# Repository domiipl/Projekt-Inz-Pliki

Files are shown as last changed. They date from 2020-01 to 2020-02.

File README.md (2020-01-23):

# Wstęp i informacje o projekcie
Cześć, jesteśmy grupą studentów, którzy na swój projekt inżynierski postanowili stworzyć niedużego robota sterowanego za pomocą interaktywnej maty.

Robot sterowany jest za pomocą sekwencji, które wprowadzamy na wyżej wymienionej macie. Możemy dawać mu proste komendy pozwalające na poruszanie się. Alternatywnym trybem jest jazda swobodna pozwalająca na sterowanie robotem w czasie rzeczywistym. Mata jest urządzeniem posiadającym układ przycisków 4x4 i ekran pokazujący aktualnie wpisywaną sekwencję. Posiadając podstawową wiedzę na temat programowania i elektroniki, będziesz mógł skonstruować taki zestaw sam, w zaciszu swojego domu. 

Bardziej szczegółowe informacje na temat samego projektu znajdziesz w samym poradniku.

Repozytorium jest podzielone na pięć folderów.
Dzielą się one na:
* **Kod robota** - znajduje się tu gotowy kod, dzięki któremu robot będzie w stanie się poruszać.
* **Kod maty** - znajduje się tu gotowy kod, dzięki któremu będziemy w stanie wysyłać komendy z maty do robota.
* **Schemat robota** - wymagane pliki do zamówienia płytki pcb do robota.
* **Schemat maty** - wymagane pliki do zamówienia płytki pcb do robota.
* **Instruktaż** - szczegółowy poradnik zawierający wymagane materiały oraz opis budowy robota i maty.

Zalecamy z zapoznaniem się dokładnie z poradnikiem przed próbą konstrukcji. Spis treści znajdziesz w pliku README w folderze "Instruktaż".

Powodzenia!

Chcielibyśmy tutaj jeszcze dodać, że wykonując projekt trzeba liczyć się z pewnymi wydatkami.
Orientacyjne koszty na dzień 16 stycznia 2020:
* **Robot** - Koszt wszystkich części robota to około 130zł, jeśli kupujemy na botlandzie. Można zmniejszyć koszta kupując części na przykład na aliexpress, jednak wydłuży to czas w jakim części do nas przyjdą.
* **Mata** - Koszt wszystkich części maty wynosi około 205zł, podobna sytuacja jak z częściami u robota, koszty można zmniejszyć kupując na przykład z allegro lub aliexpress.

Zdjęcia końcowe produktów:

**Robot**

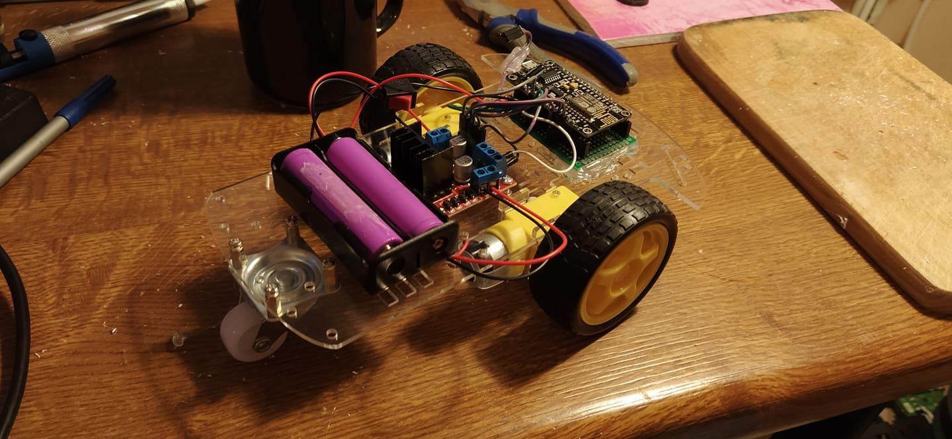
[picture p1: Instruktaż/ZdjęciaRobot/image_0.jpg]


**Mata**

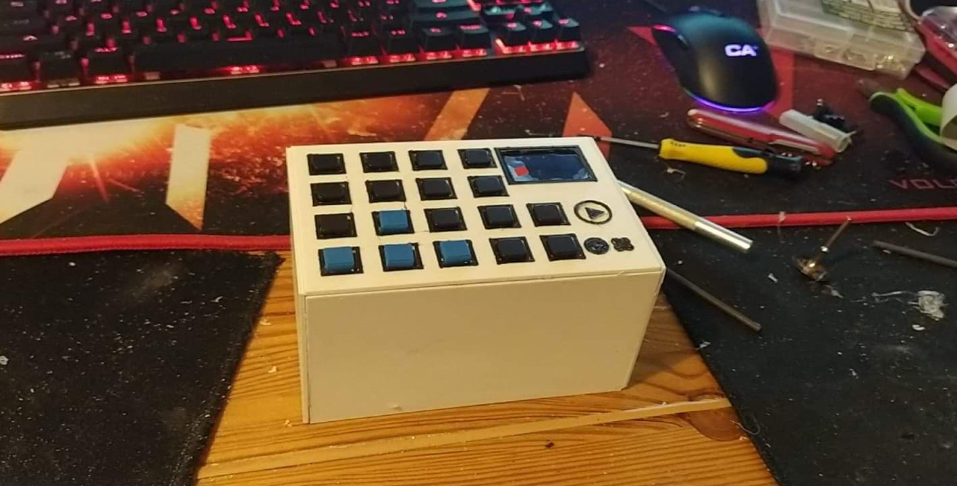
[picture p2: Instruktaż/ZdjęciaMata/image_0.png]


Filmy przedstawiające działanie projektu:

[Tryb komend](https://www.youtube.com/watch?v=S5_3_hodGV8)

[Tryb swobodny](https://www.youtube.com/watch?v=uaEHo7fgwFo)

W razie problemów, możesz kontaktować się z nami pod tym adresem e-mail:
## **projektinzrobot@gmail.com**

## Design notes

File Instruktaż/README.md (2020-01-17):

### Zalecamy czytanie poradnika zgodnie z kolejnością spisu treści

# Spis treści
1. [Informacje o projekcie](https://github.com/domiipl/Projekt-Inz-Pliki/blob/master/Instrukta%C5%BC/Informacje.md)
2. [Przygotowanie](https://github.com/domiipl/Projekt-Inz-Pliki/blob/master/Instrukta%C5%BC/Przygotowanie.md)
    - NodeMCU(Arduino)
      - Arduino IDE
      - Konfiguracja IDE
    - Raspberry Pi Zero
      - Instalacja Node.js
    - Części do budowy robota oraz maty
    - Płytki PCB
      - Schematy
      - Wymagane materiały
      - Tworzenie płytki
    - Pistolet do kleju
    - Lutownica kolbowa
    - Śrubokręt i śrubki
3. [Robot](https://github.com/domiipl/Projekt-Inz-Pliki/blob/master/Instrukta%C5%BC/Robot.md)
    - Lista wymaganych materiałów
    - Budowa Robota
    - Kod do robota
        - Instalacja kodu
        - Opis kodu
4. [Mata](https://github.com/domiipl/Projekt-Inz-Pliki/blob/master/Instrukta%C5%BC/Mata.md)
    - Lista wymaganych materiałów
    - Budowa maty
      - Obudowa maty
    - Kod do maty
      - Instalacja kodu
      - Opis kodu
5. [Połączenie](https://github.com/domiipl/Projekt-Inz-Pliki/blob/master/Instrukta%C5%BC/Po%C5%82%C4%85czenie.md)
    - Opis działania
6. [Podsumowanie](https://github.com/domiipl/Projekt-Inz-Pliki/blob/master/Instrukta%C5%BC/Podsumowanie.md)
    - Dodatkowe pomysły

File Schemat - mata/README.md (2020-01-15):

# Pliki potrzebne podczas zamawiania płytek PCB przez internet.
**Najważniejszym jest plik spakowany, ponieważ zawiera kilka istotnych plików do zamówienia internetowego.**

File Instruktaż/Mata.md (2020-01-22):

# 4. **Mata sterująca**



## **Lista wymaganych materiałów:**

1. **Raspberry Pi Zero W 512MB RAM - WiFi + BT 4.1** - 1 sztuka
<p align="center">
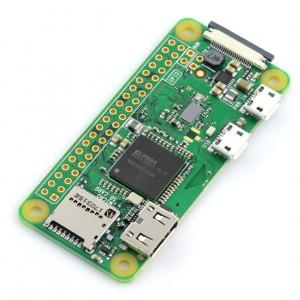
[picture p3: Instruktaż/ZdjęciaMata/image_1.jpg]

</p>

**Przykładowy link do sklepu:**

[https://botland.com.pl/pl/moduly-i-zestawy-raspberry-pi-zero/8330-raspberry-pi-zero-w-512mb-ram-wifi-bt-41.html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](https://botland.com.pl/pl/moduly-i-zestawy-raspberry-pi-zero/8330-raspberry-pi-zero-w-512mb-ram-wifi-bt-41.html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) 

[https://botland.com.pl/pl/gniazda-szpilkowe-goldpin/12659-wtyk-goldpin-2x20-prosty-raster-254mm.html](https://botland.com.pl/pl/gniazda-szpilkowe-goldpin/12659-wtyk-goldpin-2x20-prosty-raster-254mm.html) 

2. **Płytka uniwersalna:**
<p align="center">
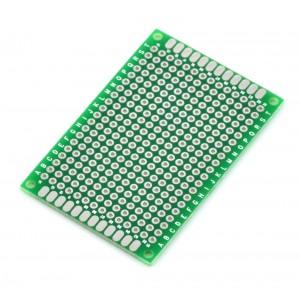
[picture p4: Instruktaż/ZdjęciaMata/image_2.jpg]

</p>

**Przykładowy link do sklepu:** 

[9cm x 15cm](https://www.gotronik.pl/uniwersalna-plytka-drukowana-pcb-9x15cm-1836-otworow-pol-kontaktowych-p-1273.html)
[2cm x 8cm](https://www.gotronik.pl/uniwersalna-plytka-drukowana-pcb-2x8cm-168-otworow-pol-kontaktowych-p-1268.html)

Wymiary minimalne:  9cm x 15cm

Komentarz: + dodatkowa 2cm x 8cm do budowy płytki zasilającej

3. **Części do płytki drukowanej:**

**Przykładowy link do sklepu:** 

[https://botland.com.pl/pl/laminaty/1054-laminat-fr4-dwustronny-rozmiar-l.html](https://botland.com.pl/pl/laminaty/1054-laminat-fr4-dwustronny-rozmiar-l.html) 

[https://botland.com.pl/pl/laminaty/1943-laminat-dwustronny-150x210mm.html](https://botland.com.pl/pl/laminaty/1943-laminat-dwustronny-150x210mm.html)[ ](https://botland.com.pl/pl/laminaty/1943-laminat-dwustronny-150x210mm.html)

[https://botland.com.pl/pl/wytrawiacze/1057-wytrawiacz-b327-100g-5901764329183.html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](https://botland.com.pl/pl/wytrawiacze/1057-wytrawiacz-b327-100g-5901764329183.html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) 

4. **Zasilanie do RPi - L7805CV** - 1 sztuka.
<p align="center">
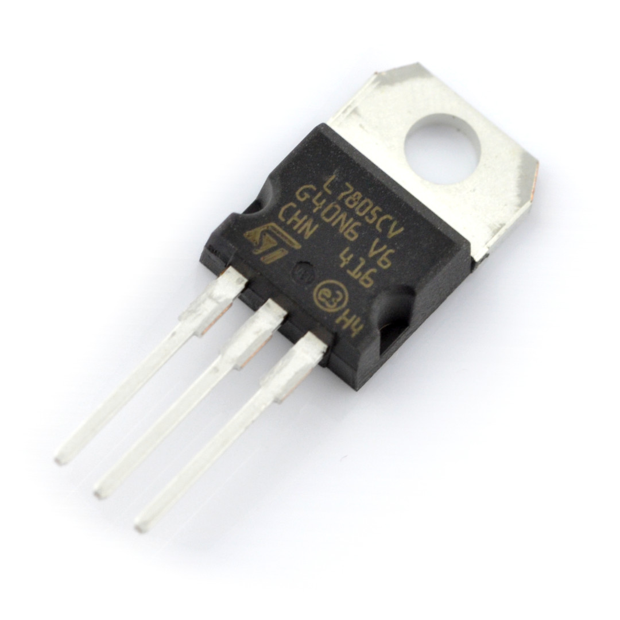
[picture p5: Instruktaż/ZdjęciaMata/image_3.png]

</p>

**Przykładowy link do sklepu:**

[https://abc-rc.pl/product-pol-6839-Elektronika-Stabilizator-L7805CV-5V-1-5A-obudowa-TO-220.html](https://abc-rc.pl/product-pol-6839-Elektronika-Stabilizator-L7805CV-5V-1-5A-obudowa-TO-220.html)

* Napięcie wyjściowe: 5V
* Maksymalne napięcie wejściowe: 35V
* Prąd wyjściowy: 1,5A
* Liczba pinów: 3
* Obudowa: TO-220
* Nr katalogowy: SNL7805CV

5. **Baterie - Model: "18650"** - 1 sztuka.
<p align="center">
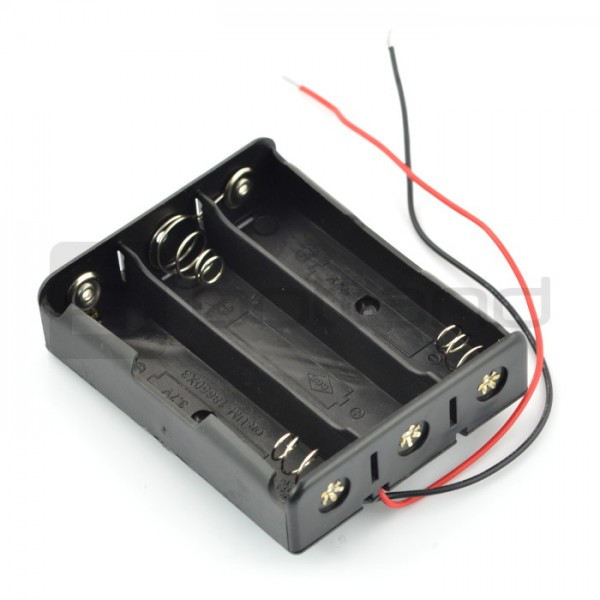
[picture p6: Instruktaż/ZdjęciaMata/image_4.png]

</p>
[https://botland.com.pl/pl/koszyki-na-baterie/5241-koszyk-na-3-baterie-typu-18650.html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](https://botland.com.pl/pl/koszyki-na-baterie/5241-koszyk-na-3-baterie-typu-18650.html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)  

[https://www.gotronik.pl/akumulator-li-ion-18650-ogniwo-litowo-jonowe-3400-mah-panasonic-ncr-18650b-p-6931.html](https://www.gotronik.pl/akumulator-li-ion-18650-ogniwo-litowo-jonowe-3400-mah-panasonic-ncr-18650b-p-6931.html)

(same baterie można dużo taniej znaleźć na Allegro lub OLX)

6. **Wtyk goldpin 2x40 prosty raster 2,54mm** - 1 raster powinien wystarczyć. 
<p align="center">
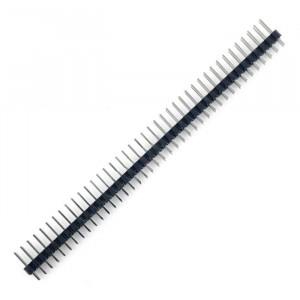
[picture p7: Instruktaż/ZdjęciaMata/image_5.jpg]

</p>

**Przykładowy link do sklepu:** 

[https://botland.com.pl/pl/gniazda-szpilkowe-goldpin/204-wtyk-goldpin-2x40-prosty-raster-254mm.html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](https://botland.com.pl/pl/gniazda-szpilkowe-goldpin/204-wtyk-goldpin-2x40-prosty-raster-254mm.html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)

7. **Tact Switch 12x12mm z nasadką**- 18 sztuk
<p align="center">
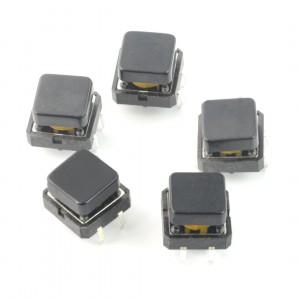
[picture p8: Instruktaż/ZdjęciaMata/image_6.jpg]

</p>

**Przykładowy link do sklepu:**

[https://botland.com.pl/pl/tact-switch/11138-tact-switch-12x12mm-z-nasadka-kwadrat-czarny-5szt.html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](https://botland.com.pl/pl/tact-switch/11138-tact-switch-12x12mm-z-nasadka-kwadrat-czarny-5szt.html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) 

8. **Wyświetlacz OLED niebieski graficzny 1,3'' 128x64px I2C v2** - 1 sztuka.
<p align="center">
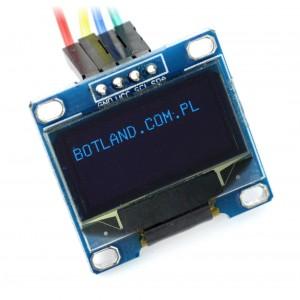
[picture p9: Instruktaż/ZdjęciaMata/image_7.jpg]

</p>

* Napięcie pracy: od 3,3 V do 5,0 V
* Sterownik: SH1106 (dokumentacja)
* Komunikacja: I2C
* Typ wyświetlacza: OLED
* Przekątna: 1,3"
* Rozdzielczość: 128 x 64 px
* Kolor znaków: biały
* Kąt widzenia: powyżej 160 °
* Temperatura pracy: od -20 °C do 70 °C
* Wymiary: 35 x 33 mm

**Przykładowy link do sklepu:**

[https://botland.com.pl/pl/wyswietlacze-oled/8246-wyswietlacz-oled-niebieski-graficzny-13-128x64px-i2c-v2-niebieskie-znaki.html](https://botland.com.pl/pl/wyswietlacze-oled/8246-wyswietlacz-oled-niebieski-graficzny-13-128x64px-i2c-v2-niebieskie-znaki.html)

## **Budowa maty**

Na wstępie chciałbym zaznaczyć, że uniwersalne płytki PCB dają nam ogromną swobodę w tym jak nasz efekt końcowy będzie się prezentować. 

Przed rozpoczęciem budowy "maty" najlepiej zapoznać się z schematem i wstępnie zaplanować sobie rozkład połączeń na uniwersalnej płytce. Porządek to podstawa, ponieważ później pozwoli nam to na łatwe modyfikacje i naprawy ewentualnych błędów.

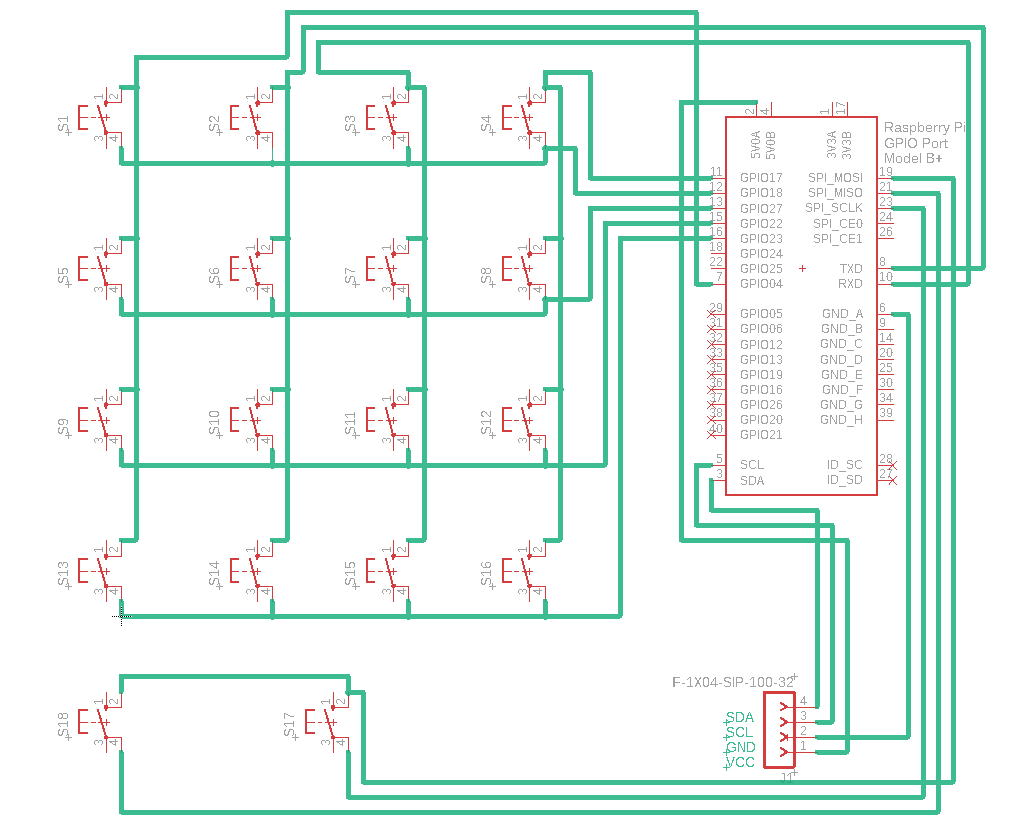
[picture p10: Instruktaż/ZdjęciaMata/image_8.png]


Pierwszym krokiem będzie rozkład przycisków S1 - S16. 

Z racji tego, że wybrana płytka jest dosyć dużych rozmiarów, bo ma aż 9cm na 15cm, to możemy pozwolić sobie na spore odstępy między przyciskami tak jak na poniższym zdjęciu (oczywiście każdy może mieć większe bądź mniejsze odstępy, to już według osobistych preferencji):

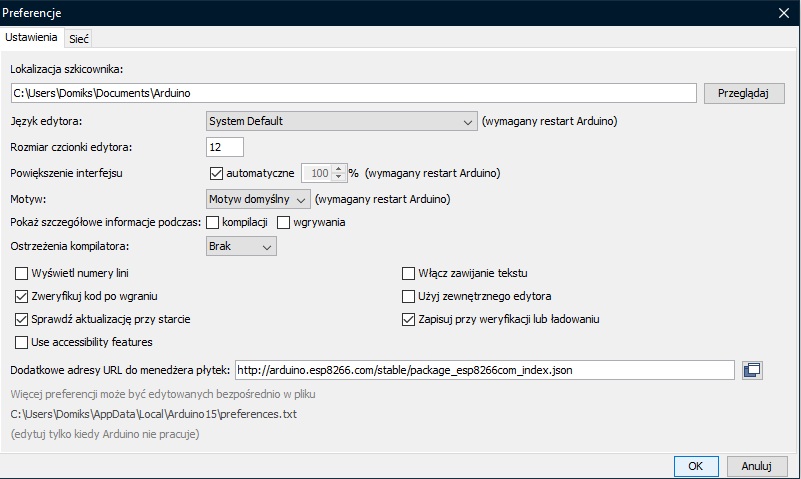
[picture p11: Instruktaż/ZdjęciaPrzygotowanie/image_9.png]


Następnie możemy dodać kolejne dwa przyciski (S17 i S18), które będą przyciskami funkcyjnymi: 



Teraz gdy już mamy zaplanowane rozłożenie przycisków możemy przejść do przypomnienia sobie schematu samej klawiatury jak i samego przycisku co ułatwi nam lutowanie. 

- Klawiatura:

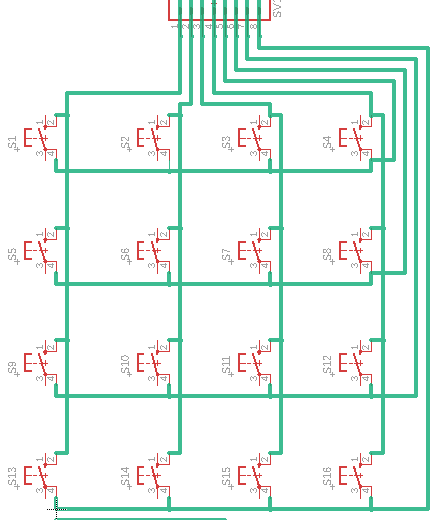
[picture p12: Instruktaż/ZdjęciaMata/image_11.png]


- Przycisk: 

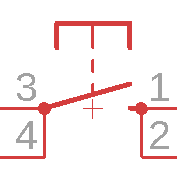
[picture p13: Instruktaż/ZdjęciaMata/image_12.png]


Podstawową rzeczą jaką powinniśmy zauważyć patrząc na schemat przycisku jest fakt, że nóżki 3 i 4 oraz 1 i 2 są ze sobą połączone, więc wciśnięcie przycisku powoduje zamknięcie obwodu między parami nóżek 1,2 i 3,4. Jest to o tyle istotny fakt, że podczas lutowania możemy zaoszczędzić bardzo dużo miejsca jak i czasu poświęconego na pracę. Przejdźmy zatem do lutowania: 

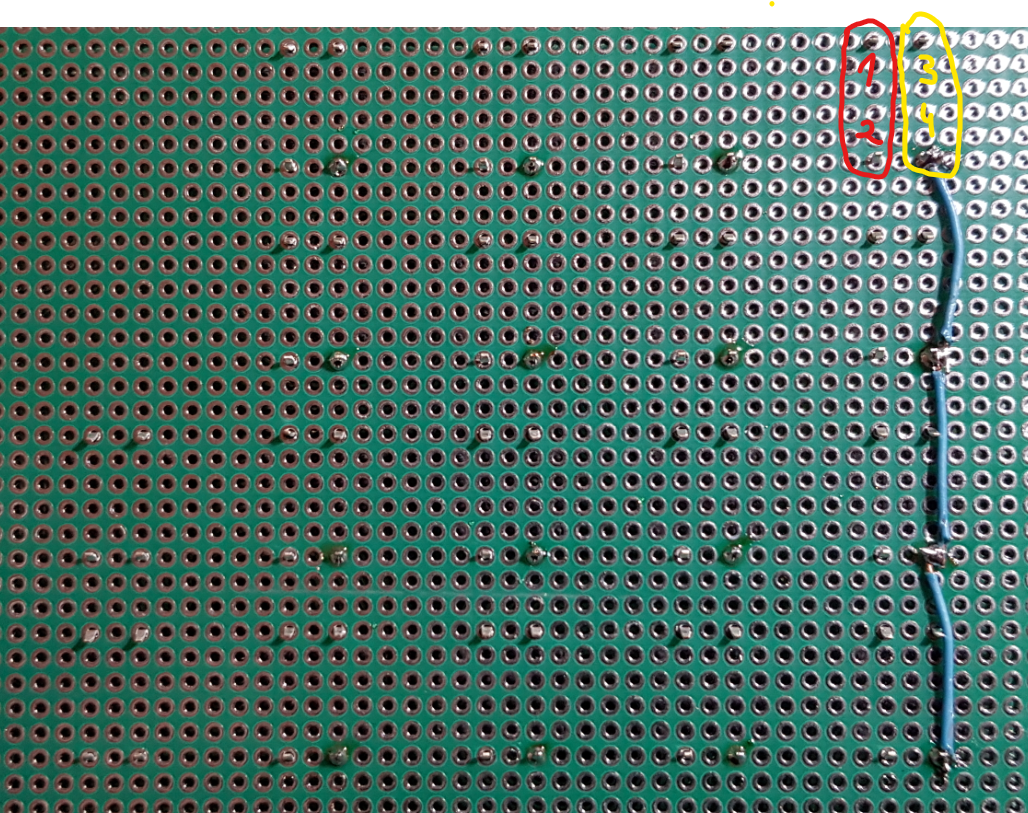
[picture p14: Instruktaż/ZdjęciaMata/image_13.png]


Na zdjęciu powyżej widzimy pierwszą zlutowaną kolumnę. Oczywiście można było zrobić to inaczej, ale tak jak wspominałem, na płytkach uniwersalnych mamy pełną dowolność.

Poniżej zdjęcia będą przedstawiać postęp w lutowaniu kolumn i wierszy między przyciskami. 







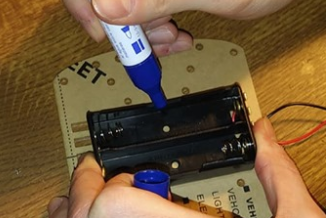
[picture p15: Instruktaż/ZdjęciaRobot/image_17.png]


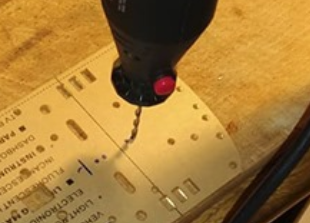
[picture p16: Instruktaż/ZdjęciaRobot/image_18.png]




Następnie aby sprawdzić czy wszystko zostało podłączone tak jak należy oraz udało nam się uniknąć "zimnych lutów" możemy na szybko podłączyć klawiaturę do np. Arduino i sprawdzić czy działa poprawnie: 

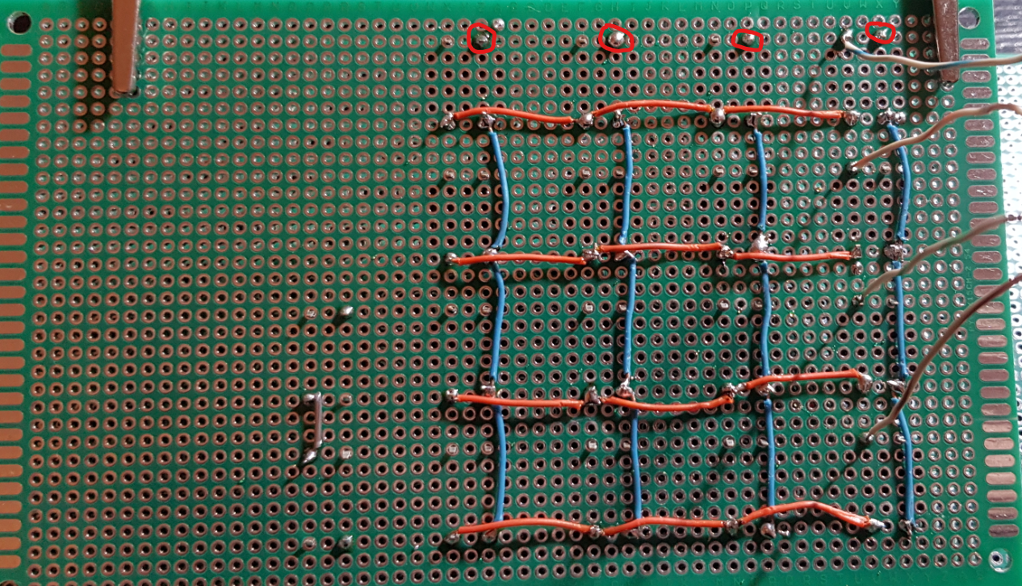
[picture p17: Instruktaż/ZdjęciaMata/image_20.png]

(Na czerwono są zaznaczone miejsca w których zostały przylutowane kable od kolumn, a nie ma ich na zdjęciu)


Powyżej widać klawiaturę podpiętą do Arduino, 

a poniżej widać program oraz wynik na konsoli po naciśnięciu klawiszy. 

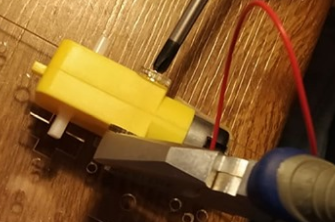
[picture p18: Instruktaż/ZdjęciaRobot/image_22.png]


(Kod do Arduino zostanie udostępniony na GitHubie jako plik [test_klawiatury_4x4](https://github.com/domiipl/Projekt-Inz-Pliki/blob/master/Kod%20-%20mata/test_klawiatury_4x4.ino))

Po poprawnych wynikach otrzymanych w teście możemy przejść do dodania pinów do klawiatury aby później można było ją podłączyć do RPi Zero. 
(Nie zastosowałem tutaj kabli przylutowanych na stałe, ponieważ nie miałem odpowiednich pod ręką, a kabelki ze skrętki nie były odpowiednie, ponieważ szybko się łamały i były zbyt sztywne)

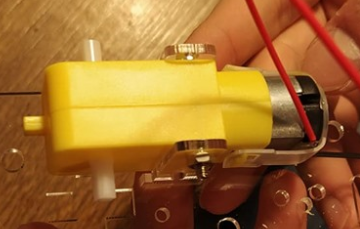
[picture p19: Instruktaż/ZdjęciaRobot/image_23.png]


Powyżej można zauważyć 4 dodatkowe piny obok przycisków funkcyjnych, ponieważ w międzyczasie został przylutowany ekran OLED co będzie widoczne na następnym zdjęciu: 


Po skończonej klawiaturze możemy przejść do zasilania jakiego użyjemy dla naszego Raspberry Pi Zero. 

Ważne jest to aby pamiętać o podstawowych parametrach jakie trzeba zapewnić RPi aby działało stabilnie. Po pierwsze najważniejsze jest napięcie, jeśli chcemy zasilić RPi poprzez złącze microUSB to musimy zapewnić następujące wartości: 

* Napięcie [V]:  4.75 - 5.25
* Natężenie [mA]: min. 500

Jest również możliwość zasilania RPi poprzez GPIO, ale jest to dosyć ryzykowny zabieg. 

Do wykonania prostego zasilacza będziemy potrzebowali: 

* L7805CV
* Koszyk na baterie 3x 18650
* kawałek płytki uniwersalnej
* trochę kabla 
* przełącznik 
* kondensator (ja wybrałem 10v 470uF)
* oraz opcjonalnie można użyć złącz ARK

Na wstępie mały obrazek z wyjściami dla L7805CV aby wszystko poprawnie podłączyć: 



Następnie schemat całego zasilacza:

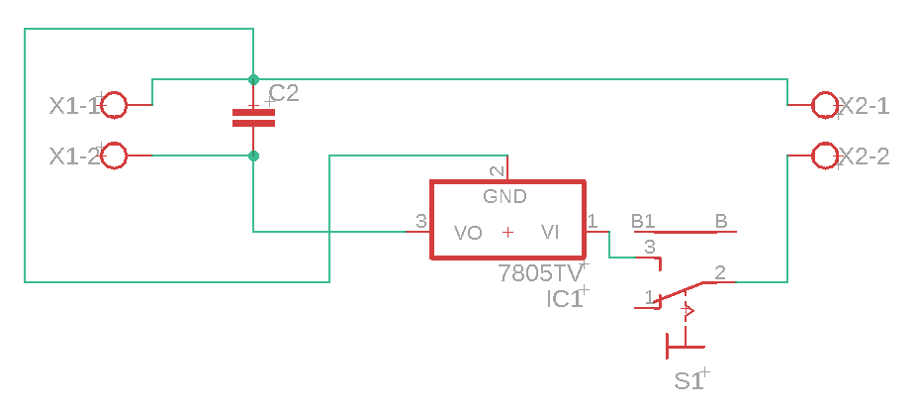
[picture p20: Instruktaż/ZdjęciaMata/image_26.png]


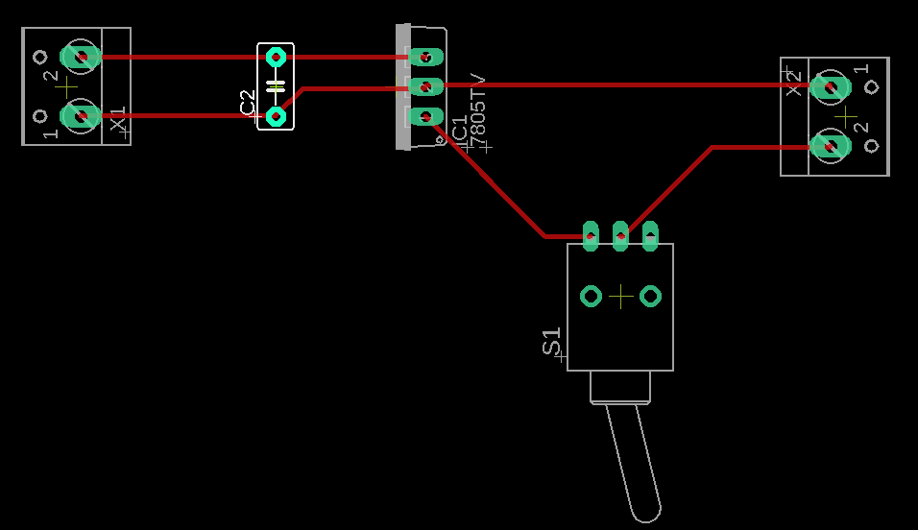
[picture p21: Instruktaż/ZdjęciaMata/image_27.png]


I końcowy wygląd: 

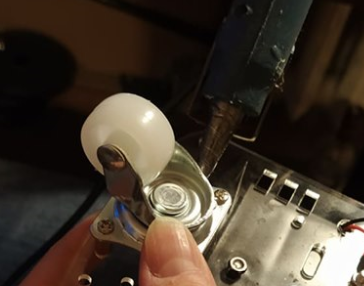
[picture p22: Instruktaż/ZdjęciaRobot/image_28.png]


Kolejna część praktycznie skończona, więc możemy przejść do kolejnych testów z udziałem Raspberry Pi Zero i naszego zasilacza. 
Na wstępie dodam jeszcze, żeby połączyć zasilacz z Raspberry użyłem starej końcówki microUSB z ładowarki która miała jedynie 2 żyły (czerwoną i czarną) przez co łatwiej było podłączyć ją pod zasilacz. 

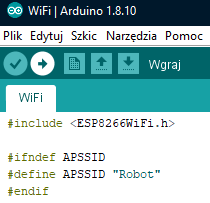
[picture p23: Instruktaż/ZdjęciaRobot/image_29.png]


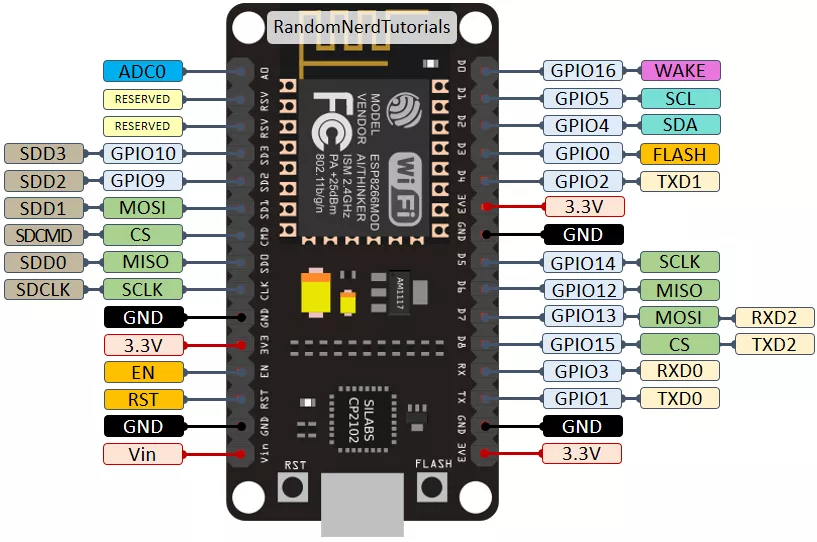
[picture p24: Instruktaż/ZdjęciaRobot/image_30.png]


Na powyższych zdjęciach widzimy pakiet 3 baterii 18650, dwa multimetry z czego jeden mierzy natężenie między zasilaczem a Raspberry (w stanie spoczynku przy uruchomionym systemie Raspbiana oraz podłączonym ekranie poprzez HDMI pobór wynosił około 290-340mA.)

Drugi multimetr (czarny) pokazuje napięcie na wyjściu zasilacza, które u mnie wynosiło 5,04 - 5,05V nawet przy większym obciążeniu RPi. Pakiet baterii na wyjściu miał napięcie w przedziale 12 - 12,10V. 

### **Obudowa maty**

Teraz możemy zostawić elektronikę na boku i przejść do budowy. 

Ja użyłem do tego plexy, ale równie dobrze możemy stworzyć obudowę z drewna lub zaprojektować i wydrukować w drukarce 3D. 

Wymiary obudowy prezentowanej na zdjęciach mają: 

* Wysokość: 70mm 
* Szerokość: 100mm
* Długość: 160mm

Oczywiście szerokość i długość można dopasować idealnie do płytki uniwersalnej i zastosować szerokość 90mm i długość 150mm. 

Zdjęć z samego wycinania nie będzie lecz przedstawię swoje osobiste doświadczenia jakie uzyskałem podczas tego procesu. 

Wskazówki: 

* Do budowy obudowy dobrze jest wykorzystać plexi o grubości 2mm, ponieważ w łatwy sposób możemy ciąć ją nożem do tapet. Po 3-4 mocniejszych nacięciach i mocniejszym nagięciu plexi powinna przełamać się. 
* Dobrze jest też nakleić sobie taśmę papierową i na niej narysować linię gdzie będziemy cięli, ponieważ plastik jest dosyć ślizgi i możemy zrobić sobie krzywdę. 
* Możemy również ciąć wzdłuż kątownika lub innej prostej rzeczy aby nóż nie uciekał na boki. tak aby nie było większych nierówności. 
* Po cięciu brzegi plexi dobrze jest wyrównać papierem ściernym. Ja użyłem 120 i 60
* Ostatnią wskazówką jest to aby nie ciąć plexi wyrzynarką, przynajmniej mi się to nie udało, ponieważ brzeszczot podczas cięcia uzyskuje wysoką temperaturę i topi plexi.

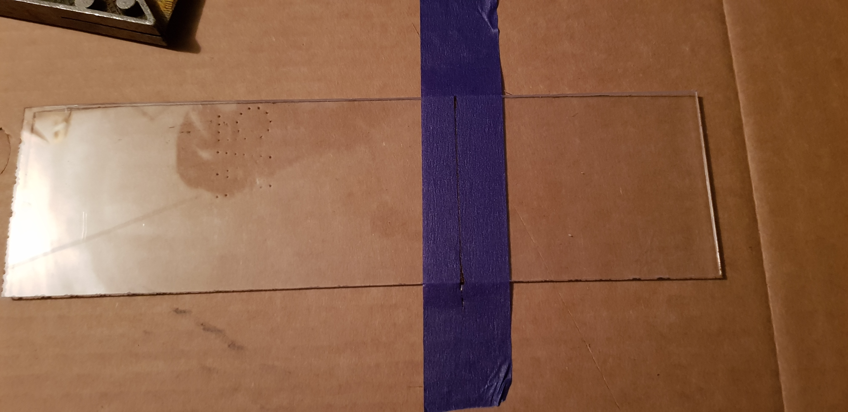
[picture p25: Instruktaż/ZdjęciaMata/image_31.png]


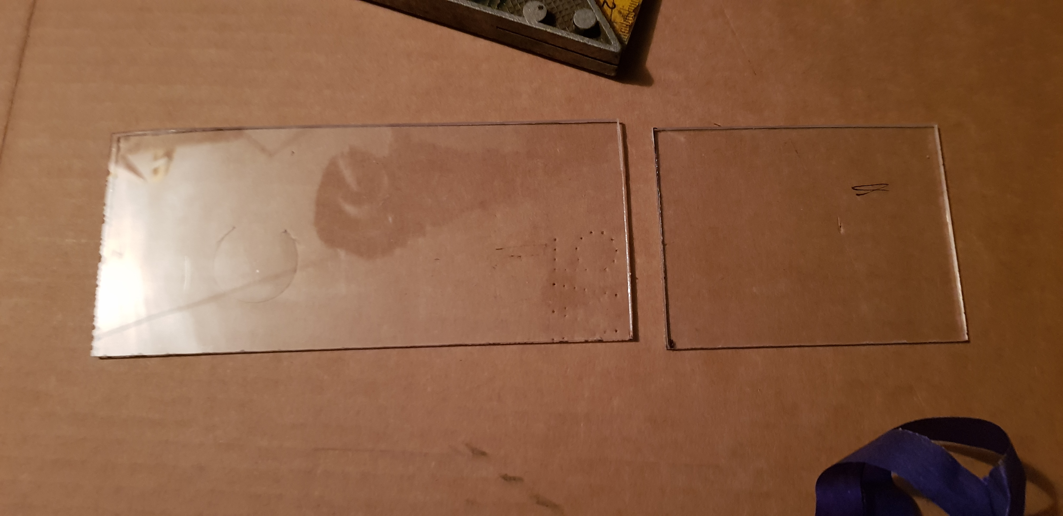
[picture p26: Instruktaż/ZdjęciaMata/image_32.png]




Do połączenia wszystkich elementów użyłem kleju na gorąco, jest on w zupełności wystarczający do tego stopnia, że jak ktoś się pomyli to praktycznie nie da się po ostygnięciu usunąć go w całości z plexi. 



Ostatnim krokiem jest połączenie wszystkich elementów razem za pomocą kabli z końcówkami żeńska-żeńska i zamknięcie całości w obudowie. Z racji tego, że moja obudowa była większa od płytki PCB, to musiałem po bokach dodać dodatkowe wsporniki aby przyczepić płytkę do obudowy. 
Efekt końcowy po podłączeniu całości i zamontowaniu przełącznika w płytce PCB. 











## **Kod do maty**

Tak jak w przypadku robota, pełny kod znajdziesz w linku poniżej, a jeżeli interesujesz się sposobem działania kodu, poniżej znajdziesz opis.

[Kod do maty](https://github.com/domiipl/Projekt-Inz-Pliki/blob/master/Kod%20-%20mata/Mata.js)

### **Instalacja kodu**

Sama instalacja kodu na Raspberry jest dość prosta. Najpierw klonujemy repozytorium - postaraj się klonować repozytorium na pulpicie. W innym przypadku może się nie zgadzać ścieżka do pliku "Mata.js" w "nodeserver.service". (Jeżeli nie chcesz klonować całego repozytorium a interesuje Cię konkretny plik - tutaj również znajdują się wszystkie pliki - [Pliki Dysk](https://drive.google.com/drive/u/1/folders/1W5VJ5BL_jayFQ0ZYsLru1H0zJjploT4B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))

```
git clone https://github.com/domiipl/Projekt-Inz-Pliki
```
Następnie przechodzimy do folderu "Projekt-Inz-Pliki" a później do folderu “Kod - mata” komendami
```
cd Projekt-Inz-Pliki
cd Kod\ -\ mata/
```
i wpisujemy 
```
sudo npm install
```
Czekamy aż zainstalują się biblioteki i wpisujemy kolejną komendę
```
sudo node Mata.js
```
Po zakończonej instalacji kodu, robimy z naszego Raspnerru serwis używając do tego pliku "nodeserver.service". Będąc dalej w folderze “Kod - mata” używamy komendy. (Uwaga - jeśli klonowałeś repozytorium w inne miejsce niż pulpit, istnieje możliwość, że możesz mieć podaną złą ścieżkę do pliku "Mata.js". W tym przypadku edytuj plik "nodeserver.service" i ustaw odpowiednią ścieżkę. Na przykład poleceniem "nano nodeserver.service")
```
sudo cp nodeserver.service /lib/systemd/system/
```
która przekopiuje plik "nodeserver.service" do folderu systemowego. W tym momencie serwis powinien działać.

**Opis kodu**

Standardowo, musimy zacząć od dołączenia odpowiednich bibliotek oraz sterowników. Będą nam potrzebne biblioteki odpowiedzialne za komunikację sieciową, komunikację z pinami malinki oraz sterownik do ekranu oled.
```
var net = require('net')
let rpio = require('rpio')
let Oled = require('sh1106-js')
```
Potrzebne będą również pewnie zmienne. Zmienna odpowiadająca za tryb robota, gdzie "0" odpowiada trybowi “drive” a “1” trybowi “freeDrive” w kodzie robota.
```
let moveMode = 0
```
Następnie zmienna, która odpowiada za aktualnie("true") i ostatnio(“false”) wciśnięty przycisk, celowo jest to maksymalnie jeden przycisk.
```
let pressed = { x: 0 , y: 0, state: false }
```
Oraz zmienna, która zawiera tablicę znaków do jazdy swobodnej ("freeDrive"). Przypisujemy przycisku do znaków,  jeżeli znak jest pusty, to nie zostanie wysłany do robota.
```
let freeDrive = [ 
  [ "", "", "", "" ],
  [ "", "", "", "" ],
  [ "", "z", "", "" ],
  [ "v", "x", "c", "" ]
]
```
Inicjalizujemy bibliotekę od Raspberry, ustawiamy opcję ekranu i je również inicjalizujemy.
```
rpio.init({

  gpiomem: false
})
var opts = {
  rpio,
  width: 128,
  height: 64,
  address: 0x3C,
  device: '/dev/i2c-1'
};
var oled = new Oled(opts)
oled.turnOnDisplay()
oled.fillRect(0, 0, 128, 64, 0)
```
Dodajemy zmienną, która odpowiada za piksele strzałek na wyświetlaczu.
```
[ // pusta
    [0, 0, 0, 0, 0, 0, 0, 0, 0, 0, 0, 0, 0, 0, 0, 0],
    [0, 0, 0, 0, 0, 0, 0, 0, 0, 0, 0, 0, 0, 0, 0, 0],
    [0, 0, 0, 0, 0, 0, 0, 0, 0, 0, 0, 0, 0, 0, 0, 0],
    [0, 0, 0, 0, 0, 0, 0, 0, 0, 0, 0, 0, 0, 0, 0, 0],
    [0, 0, 0, 0, 0, 0, 0, 0, 0, 0, 0, 0, 0, 0, 0, 0],
    [0, 0, 0, 0, 0, 0, 0, 0, 0, 0, 0, 0, 0, 0, 0, 0],
    [0, 0, 0, 0, 0, 0, 0, 0, 0, 0, 0, 0, 0, 0, 0, 0],
    [0, 0, 0, 0, 0, 0, 0, 0, 0, 0, 0, 0, 0, 0, 0, 0],
    [0, 0, 0, 0, 0, 0, 0, 0, 0, 0, 0, 0, 0, 0, 0, 0],
    [0, 0, 0, 0, 0, 0, 0, 0, 0, 0, 0, 0, 0, 0, 0, 0],
    [0, 0, 0, 0, 0, 0, 0, 0, 0, 0, 0, 0, 0, 0, 0, 0],
    [0, 0, 0, 0, 0, 0, 0, 0, 0, 0, 0, 0, 0, 0, 0, 0],
    [0, 0, 0, 0, 0, 0, 0, 0, 0, 0, 0, 0, 0, 0, 0, 0],
    [0, 0, 0, 0, 0, 0, 0, 0, 0, 0, 0, 0, 0, 0, 0, 0],
    [0, 0, 0, 0, 0, 0, 0, 0, 0, 0, 0, 0, 0, 0, 0, 0],
    [0, 0, 0, 0, 0, 0, 0, 0, 0, 0, 0, 0, 0, 0, 0, 0]
  ],

  [ // góra
    [0, 0, 0, 0, 0, 0, 0, 0, 0, 0, 0, 0, 0, 0, 0, 0],
    [0, 0, 0, 0, 0, 1, 1, 1, 1, 1, 1, 0, 0, 0, 0, 0],
    [0, 0, 0, 0, 1, 1, 1, 0, 0, 1, 1, 1, 0, 0, 0, 0],
    [0, 0, 0, 1, 1, 1, 0, 0, 0, 0, 1, 1, 1, 0, 0, 0],
    [0, 0, 1, 1, 1, 0, 0, 0, 0, 0, 0, 1, 1, 1, 0, 0],
    [0, 1, 1, 1, 0, 0, 1, 0, 0, 1, 0, 0, 1, 1, 1, 0],
    [0, 1, 1, 0, 0, 1, 1, 0, 0, 1, 1, 0, 0, 1, 1, 0],
    [0, 1, 1, 1, 1, 1, 1, 0, 0, 1, 1, 1, 1, 1, 1, 0],
    [0, 1, 1, 1, 1, 1, 1, 0, 0, 1, 1, 1, 1, 1, 1, 0],
    [0, 1, 1, 1, 1, 1, 1, 0, 0, 1, 1, 1, 1, 1, 1, 0],
    [0, 1, 1, 1, 1, 1, 1, 0, 0, 1, 1, 1, 1, 1, 1, 0],
    [0, 0, 1, 1, 1, 1, 1, 0, 0, 1, 1, 1, 1, 1, 0, 0],
    [0, 0, 1, 1, 1, 1, 1, 0, 0, 1, 1, 1, 1, 0, 0, 0],
    [0, 0, 0, 0, 1, 1, 1, 0, 0, 1, 1, 1, 0, 0, 0, 0],
    [0, 0, 0, 0, 0, 1, 1, 1, 1, 1, 1, 0, 0, 0, 0, 0],
    [0, 0, 0, 0, 0, 0, 0, 0, 0, 0, 0, 0, 0, 0, 0, 0]
  ],
```
Pozwolę sobie nie wklejać tu jeszcze tablic dla strzałki "w dół", “w lewo” oraz “w prawo”. 

Następnie funkcje, dzięki którym odpowiednio narysujemy dany symbol na wyświetlaczu.
```
function drawSymbol(x, y, arr) {
  let tab = []
  for(let i in arr) {
    for(let j in arr[i]) {
      tab.push([(parseInt(x)+parseInt(j)), (parseInt(y)+parseInt(i)), arr[i][j]])
    }
  }
  oled.drawPixel(tab)
}
function drawButtonSymbol(i, j, id) {
  let x = j * 15 + 1
  let y = i * 15 + 1
  drawSymbol(x, y, symbols[id])
}
var font = require('oled-font-5x7');
```
Teraz odpowiednio przypisujemy piny malinki. Dla rzędów i kolumn,
```
let ROWS = [11, 10, 8, 7]
let COLS = [12, 13, 16, 15]
```
oraz dla dodatkowych przycisków (Start, Zmień tryb).
```
let EROWS = [21, 23]
let ECOL = 19
```
Potrzebna będzie jeszcze tablica znaków odpowiadających za ruchy,
```
let states = ['', 'u', 'd', 'l', 'r']
```
oraz tablica reprezentująca wartości maty z tablicy wyżej (states).
```
let values = [
  ['', '', '', ''],
  ['', '', '', ''],
  ['', '', '', ''],
  ['', '', '', '']
]
```
Istotnym jest również sprawdzenie, czy znaleziono robota, dlatego tworzymy zmienną "strażnik", która to sprawdza.
```
let connected = false
```
Następnie tworzymy klienta do wysyłania i odbierania socketów.
```
client = new net.Socket();
client.connect(12345, '192.168.1.200', function() {
    console.log('Connected')
  connected = true
})
```
Tworzymy tablicę, która będzie nas informować o tym czy przycisk jest wciśnięty. ("0" - nie, “1”- tak)
```
let buttons = [
  [0, 0, 0, 0],
  [0, 0, 0, 0],
  [0, 0, 0, 0],
  [0, 0, 0, 0]
]
```
Oraz identyczna tablica dla dwóch dodatkowych przycisków.
```
let buttons2 = [0, 0]
```
Następnie inicjalizujemy piny odpowiedzialne za klawiaturę 4x4,
```
for(let i in ROWS) {
  console.log("row: " + ROWS[i])
  rpio.open(ROWS[i], rpio.INPUT, rpio.PULL_DOWN)
}
for(let i in COLS) {
  rpio.open(COLS[i], rpio.OUTPUT, rpio.LOW)
}
```
oraz klawiaturę 2x1.
```
for(let i in EROWS) {
  console.log("erow: " + ROWS[i])
  rpio.open(EROWS[i], rpio.INPUT, rpio.PULL_DOWN)
}
rpio.open(ECOL, rpio.OUTPUT, rpio.LOW)
console.log("Initialised")
```
Uruchamiamy główną pętle programu.
```
checkPins()
```
Przechodzimy do głównej funkcji programu.
```
function checkPins() {
```
Najpierw dodajemy obsługę klawiatury 4x4
```
for(let i in COLS) {
    rpio.write(COLS[i], rpio.HIGH)
    for(let j in ROWS) {
      if(rpio.read(ROWS[j]) == 1) {
        if(buttons[j][i] == 0) {
          buttons[j][i] = 1
          pushButton(j, i)
        }
        else {
          pressedButton(j, i)
        }
      }
      else if(buttons[j][i] == 1) {
        buttons[j][i] = 0
        releaseButton(j, i)
      }
    }
    rpio.write(COLS[i], rpio.LOW)
  }
```
oraz klawiatury 2x1.
```
rpio.write(ECOL, rpio.HIGH)
  for(let i in EROWS) {
    if(rpio.read(EROWS[i]) == 1) {
      if(buttons2[i] == 0) {
        buttons2[i] = 1
        pushExtraButton(i)
      }
    }
    else if(buttons2[i] == 1) {
      buttons2[i] = 0
      releaseExtraButton(i)
    }
  }
  rpio.write(ECOL, rpio.LOW)
  //cycle++
  setTimeout(function(){ checkPins() }, 1)
}
```
Potrzebna jest również funkcja, która wykonuje się po wciśnięciu przycisku przez użytkownika. Funkcja ta dostaje odpowiedni znak, w zależności który przycisk został wciśnięty i następnie rysuje odpowiedni symbol na ekranie.
```
function pushButton(i, j) {
  console.log("Button (" + i + ", " + j + ") pushed")
  if (moveMode == 0) {
    let id = states.indexOf(values[i][j])
    id++
    if(id == states.length) {
      id = 0
    }
    values[i][j] = states[id]
    drawButtonSymbol(i, j, id)
    console.log("Values after (" + i + "," + j +") press: \n" + values)
  }
  else if(moveMode == 1) {
    if(pressed.state == false) {
      pressed.x = i
      pressed.y = j
      pressed.state = true
      if(freeDrive[i][j] != "") {
        client.write(freeDrive[i][j])
      }
    }
  }
}
```
Następnie potrzebujemy funkcji, która będzie się wykonywać kiedy przycisk z klawiatury 4x4 zostanie wciśnięty i przytrzymany w tym stanie. Funkcja ta służy do trybu jazdy swobodnej.
```
function pressedButton(i, j) {
  if(moveMode == 1 && false) {
    if(pressed.x == i && pressed.y == j) {
      if(freeDrive[i][j] != "") {
        client.write(freeDrive[i][j])
      }
    }
    else if(pressed.state == false) {
      pressed.x = i
      pressed.y = j
      pressed.state = true
    }
  }
}
```
Kolejna z funkcji, wykona się po puszczeniu trzymanego przycisku z klawiatury 4x4.
```
function releaseButton(i, j) {
  if(pressed.x == i && pressed.y == j && pressed.state) {
    pressed.state = false
    if(freeDrive[i][j] != "") {
      client.write("s")
    }
  }
  console.log("Button (" + i + ", " + j + ") released")
}
```
Dodatkowo funkcja, która przywraca narysowane strzałki. TU BĘDZIE ZMIANA
```
function drawActualArrows() {
  for(let i in values) {
    for(let j in values[i]) {
      let id = states.indexOf(values[i][j])
      if(id != -1) {
        drawButtonSymbol(i, j, id)
      }
    }
  }
}
```
Przedostatnia z funkcji, która wykonuje się po wciśnięciu przycisku z klawiatury 2x1. Odpowiedzialna za zmianę trybu oraz przycisku start.
```
function pushExtraButton(i) {
  console.log("Extra button(" + i + ") pushed")
  if(i == 1) {
    if(moveMode == 0) {
      moveMode = 1
      oled.fillRect(0, 0, 128, 64, 0)
    }
    else {
      moveMode = 0
      oled.fillRect(0, 0, 128, 64, 0)
      values = [
        ['', '', '', ''],
        ['', '', '', ''],
        ['', '', '', ''],
        ['', '', '', '']
      ]
    }
  }
  else if(i == 0) { //start button
    let s = ''
    for(let i in values) {
      for(let j in values[i]) {
        s += values[i][j]
      }
    }
    client.write(s)
    console.log("TCP packet sent: " + s)
  }
}
```
Na koniec funkcja, wykonująca się po puszczeniu przycisku z klawiatury 2x1.
```
function releaseExtraButton(i) {
  console.log("Extra button (" + i + ") released")
}
```

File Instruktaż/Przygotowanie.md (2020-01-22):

# 2. **Przygotowanie.**

Do utworzenia naszego projektu, będą potrzebne: 

## **NodeMCU(Arduino)**



**ESP8266** jest popularnym mikrokontrolerem z wbudowanym WiFi. Dzięki atrakcyjnej cenie i dużym możliwościom stał się bardzo popularny, zwłaszcza w zakresie automatyki domowej. 

Moduł **NodeMCU** to **Arduino** z wlutowanym **ESP8266-12**. Arduino pozwala nam sterować pozostałymi częściami elektronicznymi w projekcie a ESP zapewnia nam bezprzewodową łączność. W naszym projekcie mikrokontroler będzie wykorzystany do sterowania robotem oraz do tworzenia sieci WiFi, do której będzie łączyć się nasza mata.

### **Arduino IDE**

Natomiast do napisania odpowiedniego oprogramowania przyda nam się **Arduino IDE**, które pozwala zaprogramować nam NodeMCU językiem C. Do poprawnego działania IDE z NodeMCU potrzebne są dodatkowe biblioteki co opiszemy w dalszej części poradnika.

Program ten jest w pełni darmowy i można go uruchomić na Windowsie, Linuxie lub Mac-Osie. Dostępny jest na przykład tutaj:

[https://www.arduino.cc/en/Main/Software](https://www.arduino.cc/en/Main/Software)



Wciskamy interesujący nas link z installerem z prawej strony i przechodzimy dalej. Ja wykorzystam tutaj instalator dla systemu Windows.



Przechodzimy dalej przyciskiem “**JUST DOWNLOAD**”.

Czekamy aż pobieranie się zakończy i przechodzimy do instalacji programu. Jeżeli nie mamy większych zastrzeżeń co do umowy licencyjnej, wciskamy "I agree" i przechodzimy dalej.



Wybieramy zawartość, którą chcemy zainstalować i przechodzimy dalej.



Następnie wybieramy folder, do którego chcemy zainstalować nasze IDE.



Po zakończonej instalacji zamykamy installer i nasze IDE jest już prawie gotowe do użytku. Musimy je jeszcze odpowiednio skonfigurować.



### **Konfiguracja IDE**

Zaczynamy od włączenia IDE, jeśli zostało przez nas wyłączone. Następnie otwieramy menu preferencji.



Kopiujemy podaną linie i wklejamy do pola "Dodatkowe adresy URL do menedżera płytek" [http://arduino.esp8266.com/stable/package_esp8266com_index.json](http://arduino.esp8266.com/stable/package_esp8266com_index.json) i potwierdzamy przyciskiem OK.



Kolejnym krokiem jest przejście do menedżera płytek.



W polu wyszukiwania wpisujemy "esp8266" a następnie instalujemy dany pakiet.



Po zakończonej instalacji pakietu, zamykamy okno menedżera płytek i klikamy jeszcze raz w narzędzia i wybieramy "NodeMCU 0.9 (ESP-Module)" z listy dostępnych płytek.



Kiedy już wybierzemy odpowiedni moduł płytki nasze IDE jest w pełni skonfigurowane i gotowe do użytku.

## **Raspberry Pi Zero**



Minikomputer Raspberry Pi w wersji miniaturowej. Wyposażony w procesor Broadcom BCM2835 1 GHz i 512 MB pamięci RAM, WiFi, Bluetooth, port miniHDMI, gniazdo microUSB OTG, 40 GPIO, złącza na kartę microSD oraz cztery otwory montażowe. Wymiary płytki to: 65 x 30 x 5 mm. Ta wersja posiada wlutowane złącza męskie GPIO.

Nasze Raspberry będzie odpowiedzialne za obsługę maty.

Przykładowy link do sklepu:

[https://botland.com.pl/pl/moduly-i-zestawy-raspberry-pi-zero/9749-raspberry-pi-zero-wh-512mb-ram-wifi-bt-41-ze-zlaczami.html](https://botland.com.pl/pl/moduly-i-zestawy-raspberry-pi-zero/9749-raspberry-pi-zero-wh-512mb-ram-wifi-bt-41-ze-zlaczami.html)

Niestety, w chwili pisania poradnika, malinka dostępna jest tylko na botlandzie lub allegro.

### **Instalacja Node.js**

Zaczynamy od wybrania odpowiedniej wersji Node’a, w naszym przypadku jest to wersja [v8.9.1](https://nodejs.org/dist/v8.9.1/?fbclid=IwAR22xwn0nsIXQ3rgm9jB1sXLJzWi_KS5BXUQsl9sqw9HL_lsmz8PQPp63Fs) i wybieramy plik "linux-armv6l", ponieważ używamy Raspberry PI Zero. Łączymy się z malinką za pomocą SSH i wpisujemy daną komendę, która pobierze nam odpowiednią wersję Node’a.
```
curl -o node-v8.9.1-linux-armv6l.tar.gz https://nodejs.org/dist/v8.9.1/node-v8.9.1-linux-armv6l.tar.gz
```
Kiedy już zakończymy pobieranie, musimy wypakować pliki używając do tego komendy
```
tar -xzf node-v8.9.1-linux-armv6l.tar.gz
```
Utworzy się nowy folder zawierający wszystkie potrzebne pliki do Node.js oraz Node Package Manager (NPM). Następnie wpisujemy komendę, która skopiuje wszystkie wypakowane pliki do odpowiedniego miejsca.
```
sudo cp -r node-v8.9.1-linux-armv6l/* /usr/local/
```
Po wykonaniu tej komendy, wszystko powinno być na swoim miejscu. W tym momencie możesz już zacząć używać Node.js. Dla pewności, można jeszcze wykonać komendę 
```
node -v
npm -v
```
Warto tutaj dodać, że wspomniany wcześniej NPM opiera się mocno o dostęp do Gita. Domyślnie Linuxowy Raspian nie nie ma zainstalowanego dostępu do Gita, dlatego warto jeszcze wykorzystać poniższą komendę.
```
sudo apt-get install git
```
W tym momencie wszystko powinno być skonfigurowane i gotowe do użytku.

Alternatywą jest pobranie gotowego obrazu [Raspberry Obraz](https://drive.google.com/drive/u/1/folders/1fIw39QTIIsRGXhbkY0WY9qPQmDjj4J0-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) i zainstalowanie go przy pomocy “win32diskimager”. W programie należy wybrać literę naszej karty SD, wybrać obraz i kliknąć Zapisz.

## **Części do budowy robota oraz maty**

Oczywiście do budowy naszego projektu będą potrzebne różne części, które opiszemy w kolejnych rozdziałach.

## **Płytki PCB**

### **Schematy**



***Zdjęcie powyżej przedstawia schemat połączeń w robocie.***



***Zdjęcie powyżej przedstawia projekt płytki drukowanej dwustronnej do robota. Czerwone linie oznaczają ścieżki na górnej warstwie laminatu, niebieskie na dolnej warstwie.***



***Zdjęcie powyżej przedstawia schemat połączeń w macie. Przyciski, ekran  oraz konektor do  Raspberry Pi.***



***Zdjęcie powyżej przedstawia projekt płytki drukowanej dwustronnej do maty. Czerwone linie oznaczają ścieżki na górnej warstwie laminatu, niebieskie na dolnej warstwie.***

Do naszego robota oraz maty będzie potrzeba po jednej płytce pcb. W tym miejscu mamy dwa sposoby na ich przygotowanie. Możesz je przygotować samemu, tak jak zrobiliśmy to my lub możesz takowe płytki zamówić za dodatkową opłatą. Jeśli zdecydujesz się zamówić płytki, będzie Ci potrzebny jedynie plik ze schematem, który musisz wysłać do odpowiedniej firmy. Najważniejszym plikiem jest plik o rozszerzeniu ".zip". Zawiera on pliki gerber, które są wymagane podczas zamówienia, jednak wstawiamy więcej plików ze schematami w przypadku gdyby były jednak potrzebne.

[Pliki do schematu maty](https://github.com/domiipl/Projekt-Inz-Pliki/tree/master/Schemat%20-%20mata)

[Pliki do schematu robota](https://github.com/domiipl/Projekt-Inz-Pliki/tree/master/Schemat%20-%20robot)

Przykładowe linki do firm: 

1. [https://jlcpcb.com/](https://jlcpcb.com/) - czas wykonania, około 3 tygodnie

2. [https://www.pcbway.com/](https://www.pcbway.com/) - czas wykonania zależy od obliczenia, mniej więcej 1,5 tygodnia

3. [https://www.fabrykapcb.pl/index.html](https://www.fabrykapcb.pl/index.html) - czas wykonania, około tygodnia

Przejdźmy teraz do przygotowania płytek w warunkach domowych. 

### **Wymagane materiały**

Potrzebne Ci będzie kilka rzeczy,

* **płyta grzejna** lub **żelazko**, najlepiej takie bez dziurek z płaską powierzchnią, inaczej płytka może się wygiąć,

* **projekt PCB**, który dostaniesz od nas

* najistotniejsza będzie jednak **drukarka laserowa**, jeśli jednak nie masz, popytaj znajomych, w punktach ksero najczęściej odmawiają - jest ryzyko przyklejenia się papieru do głowicy,

* **cienki papier kredowy**
[https://www.ebiuromax.pl/papier-kredowy-a4-135g-50-blyszczacy.html](https://www.ebiuromax.pl/papier-kredowy-a4-135g-50-blyszczacy.html)
[https://biurwa.pl/papier-kredowy-kreska-a4-130g](https://biurwa.pl/papier-kredowy-kreska-a4-130g) 

* mała **wiertarka modelarska**, najlepiej z **tytanowymi** wiertłami o szerokości **1mm**,
[https://botland.com.pl/pl/wiertarki-i-wkretarki/665-miniwiertarka-velleman-vthd01-z-akcesoriami-5410329377823.html](https://botland.com.pl/pl/wiertarki-i-wkretarki/665-miniwiertarka-velleman-vthd01-z-akcesoriami-5410329377823.html)
[https://abc-rc.pl/product-pol-7932-Mini-Wiertarka-modelarska-Szlifierka-12V-Velleman-VTHD01.html](https://abc-rc.pl/product-pol-7932-Mini-Wiertarka-modelarska-Szlifierka-12V-Velleman-VTHD01.html) 

* **kwas b327** (nadsiarczan sodowy),
[https://botland.com.pl/pl/wytrawiacze/1057-wytrawiacz-b327-100g-5901764329183.html](https://botland.com.pl/pl/wytrawiacze/1057-wytrawiacz-b327-100g-5901764329183.html)
[https://abc-rc.pl/product-pol-10124-Wytrawiacz-do-plytek-drukowanych-B327-Nadsiarczan-sodowy.html](https://abc-rc.pl/product-pol-10124-Wytrawiacz-do-plytek-drukowanych-B327-Nadsiarczan-sodowy.html) 

* **aceton**,
[https://www.ichemia.pl/37,aceton-99-9-hybrydy-250-ml.html](https://www.ichemia.pl/37,aceton-99-9-hybrydy-250-ml.html)
aceton możemy kupić spokojnie na allegro - nie ma zbyt dużego wyboru, potrzebujemy czysty aceton, w niedużej ilości, wystarczy nawet 100ml. 
Zamiast acetonu możemy użyć **IPA - alkohol izopropylowy**.
[https://botland.com.pl/pl/smary-i-oczyszczacze/974-kontakt-ipa-plus-oliwiarka-100ml-5901764329930.html](https://botland.com.pl/pl/smary-i-oczyszczacze/974-kontakt-ipa-plus-oliwiarka-100ml-5901764329930.html)
[https://abc-rc.pl/product-pol-9033-Izopropanol-AG-Kontakt-IPA-plus-100ml.html](https://abc-rc.pl/product-pol-9033-Izopropanol-AG-Kontakt-IPA-plus-100ml.html) 
Ostatecznie możemy użyć zmywacza do paznokci zawierającego aceton. Dzisiaj często zmywacze są z odżywkami i zawierają jedynie śladowe ilości acetonu, ale jeśli znajdziemy/mamy dostęp do takiego bez odżywek, będzie wystarczająco dobry do wyczyszczenia płytki.

* **miedziane tulejki 0.9mm**,
[https://www.gotronik.pl/tulejki-miedziane-0-90mm-do-wykonywania-przelotek-p-4945.html](https://www.gotronik.pl/tulejki-miedziane-0-90mm-do-wykonywania-przelotek-p-4945.html)
tulejki możemy również kupić na allegro - trzeba jedynie pamiętać aby były **miedziane **o średnicy **0.9mm**

* przyda się również **gąbka druciana** lub  **papier ścierny** o gradacji (ziarnistości) większej niż 600
[https://www.castorama.pl/papier-wodoodporny-condor-230-x-280-mm-gradacja-800-id-85959.html](https://www.castorama.pl/papier-wodoodporny-condor-230-x-280-mm-gradacja-800-id-85959.html)
[https://www.leroymerlin.pl/narzedzia-reczne/materialy-scierne-szczotki-druciane/materialy-scierne-ciete-i-w-arkuszach/papier-scierny-wodny-p800-230-x-280-mm-dexter,p453983,l810.html](https://www.leroymerlin.pl/narzedzia-reczne/materialy-scierne-szczotki-druciane/materialy-scierne-ciete-i-w-arkuszach/papier-scierny-wodny-p800-230-x-280-mm-dexter,p453983,l810.html) 

* **marker permamentny**,
[https://botland.com.pl/pl/markery/952-marker-permanentny-czarny-pentel-n850-4902506071361.html](https://botland.com.pl/pl/markery/952-marker-permanentny-czarny-pentel-n850-4902506071361.html)
[https://abc-rc.pl/product-pol-9594-Marker-do-rysowania-sciezek-0-3mm-czarny.html](https://abc-rc.pl/product-pol-9594-Marker-do-rysowania-sciezek-0-3mm-czarny.html) 

* **gumowe rękawiczki** - kwas, który będziemy używać nie jest groźny przy kontakcie ze skórą. Nie zmienia to faktu, że lepiej zachować ostrożność.

Zanim przejdziesz już do tworzenia płytki, pamiętaj aby zachować wszelką ostrożność! Powinieneś znajdować się w dobrze wentylowanym pomieszczeniu.

### **Tworzenie płytki**

**Drukowanie**

W tym kroku jest nam potrzebna drukarka laserowa. Jak wspomniałem wyżej, jeśli masz - świetnie, jeśli jednak nie, popytaj znajomych. Musimy wydrukować schemat płytki, najlepiej żebyś to zrobił przy użyciu papieru kredowego - jest tani i łatwo dostępny, także nie powinieneś mieć problemu z dostaniem go. Majac uruchomiony edytor schematow, na przykład Eagle, wybierasz kategorie FILE a nastepnie RUN, wtedy program odczytuje folder zawierajacy skrypty w katalogu ULP. Jeden ze skryptow jest tak napisany,ze umozliwia wydrukowanie korzystajac z drukarki np. na folii widoku sciezek warstwy TOP, BOTTOM, SOLDER. Warstwy te sa drukowane osobno na kazdej kartce papieru lub folii. Umozliwia to wykonanie w warunkach domowych plytki drukowanej. Wykorzystujemy do tego plik [V5.brd](https://github.com/domiipl/Projekt-Inz-Pliki/blob/master/Schemat%20-%20mata/V5.brd) dla płytki od maty oraz 
[Robot_v2.brd](https://github.com/domiipl/Projekt-Inz-Pliki/blob/master/Schemat%20-%20robot/Robot_V6.brd) dla płytki robota.



**Wymiarowanie**

Teraz przykładamy schemat do płytki i wiercimy dziurki w rogach schematu na płytce, tak aby góra i dół pokrywały się ze sobą, ponieważ płytka będzie dwustronna. Następnie docinamy płytkę do wielkości schematu i przechodzimy do kolejnego kroku.







**Czyszczenie powierzchni**

Powierzchnię płytki należy oczyścić przed wykonaniem kolejnych czynności. Odbywa się to w dwóch krokach. Najpierw szlifujemy lekko powierzchnię z obu stron płytki używając papieru ściernego lub druciaka. Po zakończonym procesie szlifowania przecieramy powierzchnię alkoholem bądź acetonem - my użyliśmy do tego starej szczoteczki do zębów maczanej w czystym acetonie.

**Nakładanie ścieżek**

Zaczynamy od rozgrzania żelazka, musi być ustawione na maksymalną temperaturę. Przyda się tutaj jakaś płaska powierzchnia jak na przykład kafelki w łazience czy kuchni albo drewniana deska do krojenia. Układamy kawałek papieru ręcznikowego lub toaletowego. Na papierze układamy płytkę, tak aby nie dotykała kafelek. Następnie na płytkę kładziemy papier kredowy z wydrukowanym schematem i ustawiamy zgodnie z wyrobionymi dziurkami. Toner powinien być ustawiony do dołu. Dokładamy kolejny kawałek papieru ręcznikowego, uważając żeby schemat na płytce nie przesunął się. Kiedy już wszystko jest ładnie ustawione, dociskamy całość rozgrzanym żelazkiem i co kilka sekund wykonujemy ruch prasowania. Cały proces powinien trwać około 5 minut.

Po zakończonym procesie nakładania, ostrożnie wyciągamy płytkę (powinieneś tu zachować ostrożność, całość może być dosyć gorąca). Następnie płytkę z przyklejonym już schematem ostrożnie odkładamy w misce i chłodzimy pod bieżącą wodą, przy okazji warto namoczyć przyklejony schemat. 
Kiedy schemat będzie już dobrze namoczony, powoli odrywamy go od płytki. Na naszej płytce powinien być obecnie widoczny toner ze ścieżkami, jeżeli dostrzegasz jakieś przerwane ścieżki, możesz je ostrożnie poprawić markerem permamentnym.

**Cały proces powtarzamy dla drugiej strony laminatu. Wywiercone wcześniej dziury pozwolą ułożyć wydruk tak, aby pokrywał się z drugą stroną.**

**Wiercenie**

Musimy teraz wywiercić małe otwory na piny. Używamy do tego naszej wiertarki modelarskiej z tytanowym wiertłem  o szerokości 1mm. Następnie w powstałe otwory wbijamy miedziane tulejki.

**Wytrawianie**

W tym miejscu powinieneś założyć swoje gumowe rękawiczki. Sam roztwór nie powinien być niebezpieczny, jednak ostrożności nigdy za wiele!

Przejdziemy teraz do utworzenia roztworu, który wytrawi miedź z płytki. Przygotuj 100 gramów kwasu B327 oraz pół litra wody (takie są proporcje roztworu), najlepiej o temperaturze 50 stopni, jeżeli nie jesteś w stanie kontrolować temperatury wody możesz ostatecznie użyć wrzątku. Zalewasz kwas ciepłą wodą i mieszasz wszystko do momentu, w którym kryształki kwasu się rozpuszczą.

Do utworzonego roztworu wrzucamy naszą płytkę. Całość najlepiej umieścić w płaskim pudełku. Kiedy płytka znajduje się w środku, potrząsaj lekko pudełkiem, tak aby mieszanka była cały czas w ruchu, ponieważ to przyspiesza proces trawienia. Całość powinna trwać od 5 do 10 minut. Po upływie około 3 minut, obróć płytkę, aby zobaczyć jak proces trawienia przebiega z drugiej strony.



Kiedy miedź zostanie usunięta z miejsc, w których nie ma toneru, proces trawienia można uznać za zakończony. Wyciągamy płytkę z mieszanki. Następnie płytkę wycieramy i myjemy pod bieżącą wodą.

Warto tutaj dodać, że jeśli planujesz zrobić więcej płytek, to roztwór jest wielokrotnego użytku, jednak z każdym użyciem będzie zmieniał kolor na coraz bardziej niebieski i proces trawienia będzie odrobinę wolniejszy.

Sprawdzamy teraz czy wszystkie ścieżki wyglądają poprawnie, jeśli tak to zmywamy toner acetonem. Miejsca, w których toner przykleił się bardzo mocno, można lekko przetrzeć papierem ściernym lub drucianą gąbką.

## **Pistolet do kleju**



Zalecane właściwości:

* Moc - 10 W,
* Średnica kleju - 8 mm,

Przykładowy link:

[https://abc-rc.pl/product-pol-11945-Pistolet-do-kleju-na-goraco-110-240V-40W-Glue-Gun.html](https://abc-rc.pl/product-pol-11945-Pistolet-do-kleju-na-goraco-110-240V-40W-Glue-Gun.html)  + [https://abc-rc.pl/product-pol-11946-Klej-do-pistoletu-na-goraco-16x1-1cm-klej-do-klejenia-na-goraco-przezroczysty.html](https://abc-rc.pl/product-pol-11946-Klej-do-pistoletu-na-goraco-16x1-1cm-klej-do-klejenia-na-goraco-przezroczysty.html)

[https://botland.com.pl/pl/kleje-i-klejarki/976-pistolet-do-klejenia-20w-zd-5.html](https://botland.com.pl/pl/kleje-i-klejarki/976-pistolet-do-klejenia-20w-zd-5.html)
[https://botland.com.pl/pl/kleje-i-klejarki/896-klej-do-pistoletu-cienki-74150-mm-przezroczysty.htmlv](https://botland.com.pl/pl/kleje-i-klejarki/896-klej-do-pistoletu-cienki-74150-mm-przezroczysty.htmlv) 

## **Lutownica kolbowa**



Zalecane właściwości:

* Napięcie zasilania - 230 V,
* Moc - 60 W,

Przykładowy link do sklepu:

[https://botland.com.pl/pl/lutownice-kolbowe/1126-lutownica-kolbowa-zd200c-oporowa-60w.html](https://botland.com.pl/pl/lutownice-kolbowe/1126-lutownica-kolbowa-zd200c-oporowa-60w.html)

[https://abc-rc.pl/product-pol-12145-Lutownica-220V-60W-regulacja-temperatury.html](https://abc-rc.pl/product-pol-12145-Lutownica-220V-60W-regulacja-temperatury.html)

## **Śrubokręt i śrubki**

* śrubokręt płaski
* śrubokręt krzyżakowy
[https://botland.com.pl/pl/zestawy-narzedzi/12640-zestaw-wkretakow-precyzyjnych-16-elementow-5900804106333.htm](https://botland.com.pl/pl/zestawy-narzedzi/12640-zestaw-wkretakow-precyzyjnych-16-elementow-5900804106333.htm)
Taki zestaw powinien w zupełności wystarczyć. Naszym zdaniem lepiej kupić taki zestaw niż kupować pojedyncze śrubokręty

* 4 śrubki M3x10mm
* 4 nakrętki M3
[https://botland.com.pl/pl/srubki-i-nakretki/636-zestaw-srubki-i-nakretki-180szt-5410329304485.html](https://botland.com.pl/pl/srubki-i-nakretki/636-zestaw-srubki-i-nakretki-180szt-5410329304485.html) 

[https://botland.com.pl/pl/srubki-i-nakretki/770-srubki-m3-dlugosc-10mm-z-podkladkami-10szt.html](https://botland.com.pl/pl/srubki-i-nakretki/770-srubki-m3-dlugosc-10mm-z-podkladkami-10szt.html)

[https://botland.com.pl/pl/srubki-i-nakretki/806-nakretki-m3-10szt.html](https://botland.com.pl/pl/srubki-i-nakretki/806-nakretki-m3-10szt.html)

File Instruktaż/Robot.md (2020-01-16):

# 3. **Robot.**



## **Lista wymaganych materiałów.**

1. **Chassis Rectangle 2WD 2-kołowe podwozie robota z napędem** – 1 sztuka 
<p align="center">

</p>
Przezroczysta platforma do budowy robota. W zestawie znajdują się dwa silniki prądu stałego z kołami o średnicy 65 mm. W części przedniej podporę stanowi metalowe koło obrotowe. Elementy podwozia są zrobione z akrylu, posiadają otwory montażowe pozwalające zamontować różnego rodzaju sensory czy kontrolery.

Zestaw zawiera:

* Platformę montażową
* Dwa koła z oponami o średnicy 65 mm 
* Dwa silniki prądu stałego z przekładniami
* Jedno metalowe koło obrotowe montowane przy pomocy dwóch śrub
* Metalowe oraz plastikowe podzespoły (śrubki, nakrętki, itp.)
* Włącznik
* Koszyk na baterie (4 x AA) ze przewodami ze zdjętą izolacją

Warto tutaj dodać, że jeśli zdecydujesz się na zakup danego podwozia, to nie musisz już martwić się o silniki oraz koła, ponieważ są zawarte w tym zestawie. Natomiast nadal powinieneś zakupić podany w tej liście koszyk na baterie.

Przykładowy link do sklepu:

[https://botland.com.pl/pl/podwozia-robotow/7283-chassis-rectangle-2wd-2-kolowe-podwozie-robota-z-napedem.html](https://botland.com.pl/pl/podwozia-robotow/7283-chassis-rectangle-2wd-2-kolowe-podwozie-robota-z-napedem.html)

[https://abc-rc.pl/product-pol-7656-Podwozie-robota-2WD-RT-5-210mm-2-silniki-podwozie-Arduino.html](https://abc-rc.pl/product-pol-7656-Podwozie-robota-2WD-RT-5-210mm-2-silniki-podwozie-Arduino.html) 

2. **Silnik DC z przekładnią 1:48** – 2 sztuki (zawarte w zestawie z podwoziem)
<p align="center">

</p>
Unikalna jednostka napędowa do Twojego robota. Silnik prądu stałego z przekładnią 1:48 zapewni wspaniałe osiągi dla Twojego robota. Dwustronna oś pozwala zamontować koło z oponą z dowolnej strony. 

3. **Koło plastikowe z oponą 65/25 mm** – 2 sztuki (zawarte w zestawie z podwoziem)
<p align="center">

</p>
Doskonała ochrona przed aquaplaningiem. Krótka droga hamowania. Bardzo dobra przyczepność na zakrętach. Niski poziom hałasu przez cały okres eksploatacji opony.

4. **Moduł dwukanałowego sterownika silników z L298N**– 1 sztuka
<p align="center">

</p>
Umożliwia on sterowanie jednocześnie dwóch silników DC lub jednego silnika krokowego. Kontroler ten pozwala ustawić stałą (pełną) prędkość obrotu kół, lub kontrolować ją sygnałem PWM.

Przykładowy link do sklepu:

[https://abc-rc.pl/product-pol-6196-Modul-sterownika-L298N-do-silnikow-DC-i-krokowych-Arduino.html](https://abc-rc.pl/product-pol-6196-Modul-sterownika-L298N-do-silnikow-DC-i-krokowych-Arduino.html) 

[https://nettigo.pl/products/modul-dwukanalowego-sterownika-silnikow-z-l298n](https://nettigo.pl/products/modul-dwukanalowego-sterownika-silnikow-z-l298n)

5. **Moduł WiFi NodeMCU V3 LoLin ESP-12E(Arduino)** – 1 sztuka
<p align="center">

</p>
Przykładowy link do sklepu:

[https://nettigo.pl/products/modul-wifi-nodemcu-v3-lolin-esp-12e](https://nettigo.pl/products/modul-wifi-nodemcu-v3-lolin-esp-12e)

[https://botland.com.pl/pl/moduly-wifi/8241-modul-wifi-esp8266-nodemcu-v3.html](https://botland.com.pl/pl/moduly-wifi/8241-modul-wifi-esp8266-nodemcu-v3.html) 

6. **Kondensator 100uF 16V lub więcej** - 1 sztuka
<p align="center">

</p>
Przykładowy link do sklepu:

[https://botland.com.pl/pl/kondensatory-elektrolityczne-tht/898-kondensator-elektrolityczny-100uf35v-6x12mm-105c-tht-10szt.html](https://botland.com.pl/pl/kondensatory-elektrolityczne-tht/898-kondensator-elektrolityczny-100uf35v-6x12mm-105c-tht-10szt.html)

[https://nettigo.pl/products/zestaw-5-kondensatorow-elektrolitycznych-100-f-35v](https://nettigo.pl/products/zestaw-5-kondensatorow-elektrolitycznych-100-f-35v) 

7. **Dwupozycyjny przełącznik MTS-102** – 1 sztuka
<p align="center">

</p>
Przełącznik dźwigniowy, dwupozycyjny, jednosekcyjny, MTS-1.

Dane techniczne:

Rodzaj napięcia AC/DC Obciążenie do 3A przy 250V Obciążenie do 6A przy 125V Wysokość: 33mm Średnica otworu montażowego: 6mm

Jeśli dostaniemy koszyk na ogniwa z włącznikiem, wtedy ta część jest nie potrzebna

Przykładowy link do sklepu:

[https://nettigo.pl/products/dwupozycyjny-przelacznik-mts-102](https://nettigo.pl/products/dwupozycyjny-przelacznik-mts-102)

[https://botland.com.pl/pl/przelaczniki-z-dzwignia/2478-przelacznik-dzwigniowy-on-on-250v3a.html](https://botland.com.pl/pl/przelaczniki-z-dzwignia/2478-przelacznik-dzwigniowy-on-on-250v3a.html)

8. **Koszyk na dwa ogniwa 18650 2S**– 1 sztuka
<p align="center">

</p>
Łączy w szereg dwa ogniwa 18650. Daje to od ~7.0 do 8.4 V w zależności od naładowania ogniw. Długi 30-centymetrowy kabel daje się ładnie układać. 

Przykładowy link do sklepu:
[https://botland.com.pl/pl/koszyki-na-baterie/5240-koszyk-na-2-baterie-typu-18650.html](https://botland.com.pl/pl/koszyki-na-baterie/5240-koszyk-na-2-baterie-typu-18650.html) 

[https://abc-rc.pl/product-pol-8528-Koszyk-na-akumulator-2x-18650-3-7V-Li-Ion-koszyczek-na-baterie-ogniwo-z-przewodami.html]
(https://abc-rc.pl/product-pol-8528-Koszyk-na-akumulator-2x-18650-3-7V-Li-Ion-koszyczek-na-baterie-ogniwo-z-przewodami.html) 

Koszyk z włącznikiem:
[https://abc-rc.pl/product-pol-12801-Koszyk-na-akumulator-2x-18650-z-wylacznikiem-koszyczek-z-pokrywa-i-przewodami.html](https://abc-rc.pl/product-pol-12801-Koszyk-na-akumulator-2x-18650-z-wylacznikiem-koszyczek-z-pokrywa-i-przewodami.html) 

9. **Stabilizator liniowy 3.3V  min. 0.8A** – 1 sztuka
<p align="center">

</p>
Przykładowy link do sklepu:

[https://nettigo.pl/products/stabilizator-liniowy-3-3v-0-8a](https://nettigo.pl/products/stabilizator-liniowy-3-3v-0-8a)

[https://botland.com.pl/pl/regulatory-napiecia/7685-stabilizator-ldo-33v-ld1117v33-tht-to220.html](https://botland.com.pl/pl/regulatory-napiecia/7685-stabilizator-ldo-33v-ld1117v33-tht-to220.html) 

## **Budowa Robota**

Będąc odpowiednio przygotowanym, możemy przejść do budowy naszego robota. 

**Przygotowanie silników**

Sprawdzamy czy w silnikach mamy zlutowane kabelki, jeśli są to przejdź do kolejnego kroku.

Zdejmujemy najpierw mały kawałek izolacji na kabelkach - około 1 do 2mm, możesz do tego użyć na przykład noża do tapet. Lekko natnij izolację i pociągnij, powinna bez problemu zejść.

Następnie potrzebujemy rozgrzać lutownicę, jeżeli posiadasz zwykłą kolbową - dotknij grotu cyną, jeśli będzie się topić to lutownica jest wystarczająco nagrzana, jeśli jednak posiadasz lutownicę z możliwością regulacji temperatury - ustaw ją w okolicach 400-450 stopni.

Na blaszkę w silniku nakładamy odrobinę cyny.



Odsłonięty kabel przykładamy do blaszki silnika - kolor kabelka jest obecnie nieistotny, polaryzację możemy zmienić później w kodzie robota.

 

Przykładamy rozgrzaną lutownicę do odsłoniętego kabelka i nakładamy cynę tak, aby rozgrzała cynę na blaszce i abyśmy mogli przełożyć kabelek przez dziurkę i pokryć go cyną. Oczywiście nie powinieneś ruszać kabelkiem w trakcie lutowania. Po krótkiej chwili lut zastygnie i połączenie będzie gotowe. Powtarzamy tą czynność dla reszty kabelków.



Jeśli korzystasz z koszyka na ogniwa, które podaliśmy w liście części, prawdopodobnie nie będzie musiał lutować kabelków. Jeśli jednak koszyk nie miałby kabli lub miałbyś inny koszyk na baterie, powtórz powyższe czynności.

**Lutowanie włącznika**

Istotnym jest jeszcze dolutowanie przycisku włączenia/wyłączenia, bez tego nasz robot się nie uruchomi. Łapiemy za koszyk na ogniwo i ucinamy czarny kabelek mniej więcej w połowie. Teraz musimy jeszcze zdjąć kawałek izolacji na końcu kabelka od koszyka oraz z obu stron na uciętym kawałku kabelka. 



Następnie przechodzimy do lutowania.



Kabelek, który został odcięty lutujemy do blaszki w  miejscu, w którym znajduje się "I" na przycisku, a w miejscu “O” powinniśmy dolutować czarny kabel, który wychodzi od koszyka na ogniwa. “I” oznacza włączony, a “O” wyłączony.





Po zakończonym lutowaniu dobrze jest wgrać kod do robota, tak dla wygody. Opis jak to zrobić znajdziesz w kolejnym dziale nazwanym "Kod do robota".

**Przygotowanie podwozia**

Musimy odpowiednio wywiercić otwory w podwoziu, tak aby móc zamontować części w odpowiednich miejscach. Przykładamy koszyki od akumulatorów i zaznaczamy markerem miejsca, w których następnie wiercimy otwory. 





Do wiercenia używamy wiertła 3mm. 

Czynności powtarzamy dla kontrolera DC. 

Na koniec odklejamy jeszcze folię zabezpieczającą podwozie.





**Montaż części**

Łapiemy za śrubokręt krzyżakowy oraz śrubki i przykręcamy do podwozia silniki w uchwytach montażowych.







Następnie montujemy części, dla których wywierciliśmy otwory w punkcie powyżej, czyli kontroler DC oraz koszyk na ogniwa.





Przykręcamy również koło obrotowe, dla którego zrobiono miejsca na przodzie podwozia.





Po zamontowaniu wszystkich części, polecamy użyć pistoletu na klej i zakleić koło obrotowe. Dzięki temu, robot będzie bardziej stabilny podczas jazdy. Uważaj tylko żeby przyklejone koło było ustawione prosto, inaczej robot będzie niepotrzebnie skręcał w trakcie jazdy.



**Połączenie części**

Zaczynamy od połączenia kabli silników do wejść na kontrolerze DC - są to skręcane, skrajne podwójne wejścia. To jak podłączysz silniki nie ma w tym momencie znaczenia. Po skończeniu robota przetestuj go i zamień w razie potrzeby kable od silników.

Następnie czas podpiąć zasilanie. Jeśli korzystasz z płytki drukowanej, na płytce masz wyprowadzone odpowiednie piny do zasilania kontrolera DC, a zasilanie Node’a idzie prosto z regulatora napięcia do odpowiednich wejść. Jeśli używasz płytki uniwersalnej, wlutuj regulator napięcia w płytkę oraz połącz ze sobą odpowiednie piny regulatora i Node’a (Regulator -> NodeMCU)

* Output -> 3.3V
* GND -> GND

Pamiętaj aby do wejścia Input regulatora podpiąć + od zasilania.
Bezpośrednio z zasilania, podłącz się kabelkami do wejść 12V i GND w DC Controlerze (Zasilanie -> DC Controller)

* 12V -> 12V
* GND -> GND

Na płytce mamy dwie sekcje po 3 piny, odpowiadające pinom D1,D2,D3 oraz D5,D6,D7 znajdującym się w NodeMCU.

Podłączamy je zgodnie z opisem poniżej (NodeMCU -> DC Controller)

* D1 -> IN4
* D2 -> IN3
* D3 -> ENA
* D5 -> IN1
* D6 -> IN2
* D7 -> ENB

Oczywiście możesz piny podłączyć w inny, np. bardziej uporządkowany sposób. Pamiętaj jednak aby nanieść zmiany w kodzie. Pamiętaj również, że piny w NodeMCU nie są numerowane w kodzie tak, jak jest to opisane na płytce. Skorzystaj np. z tego schematu by sprawdzić piny:



## **Kod do robota**

Cały, gotowy do wgrania kod do robota znajdziesz pod tym linkiem:

[Kod do robota](https://github.com/domiipl/Projekt-Inz-Pliki/blob/master/Kod%20-%20robot/Robot.ino)

**Instalacja kodu**

Pobierz plik z kodem i otwórz go w Arduino IDE. Następnie podłącz robota do swojego komputera. Mając otwarty plik z kodem w IDE oraz podłączonego robota, wciśnij ikonę strzałki w programie i poczekaj aż kod zostanie wgrany do robota.



A jeśli interesuje Cię co się w tym kodzie znajduje, poniżej opiszę kod krok po kroku.

**Opis kodu**

Zacznijmy od dołączenia odpowiedniej biblioteki, która odpowiedzialna będzie za obsługę ESP8266.
```
#include <ESP8266WiFi.h>
```
Następnie definiujemy nazwę sieci, jeśli zmienna APSSID, w której umieszczamy nazwę naszej sieci nie jest zdefiniowana, to deklarujemy ją warunkowo.
```
#ifndef APSSID 
#define APSSID "Robot"
#endif
```
I powtarzamy czynność dla zmiennej PORT.
```
#ifndef PORT 
#define PORT 12345
#endif
```
Przechodzimy do zdefiniowania zmiennej odpowiedzialnej za przechowywanie serwera.
```
WiFiServer server(PORT); 
const char *ssid = APSSID;
```
Na koniec definiujemy zmienne odpowiadające za piny do silników, prędkość, czas jazdy pojazdu i diodę LED.
```
int IN1=12;   
int IN2=14;   
int IN3=4;    
int IN4=5;    
int ENA=0;    
int ENB=13;   
int multi_=1;  
int time_=250;
int led=2;
```
Musimy teraz napisać funkcje odpowiedzialne za sterowanie robotem w obu trybach, więc  przejdziemy do napisania pierwszej z funkcji odpowiedzialnej za sterowanie robotem. Funkcja będzie przyjmować argumenty odpowiedzialne za stany silników, mnożnik prędkości oraz czas poruszania.
```
void drive(int I1, int I2, int I3, int I4, int multi, int t){
```
Następnie zapisujemy ustawienia stanów silników.
```
digitalWrite(IN1,I1);
digitalWrite(IN2,I2);
digitalWrite(IN3,I3);
digitalWrite(IN4,I4);
```
I przechodzimy do napisania pętli odpowiedzialnej za płynne rozpędzanie naszego pojazdu.
```
Serial.println("Akceleracja:");
for(int i = 0; i < 1024; i += multi){
```
Ustawiamy prędkości silników.
```
analogWrite(ENA,i);
analogWrite(ENB,i);
Serial.print(i);
Serial.print("...");
delay(1);
}
```
Skoro już rozpędziliśmy naszego robota, musimy teraz napisać pętlę odpowiedzialną za jego płynne hamowanie.
```
delay(t);
Serial.println("Hamowanie:");
for(int i = 1024; i > 0; i -= multi){
```
Tak jak przy rozpędzaniu, ustawiamy prędkości silników również przy hamowaniu i kończymy jedną z funkcji odpowiedzialną za sterowanie.
```
analogWrite(ENA,i);
analogWrite(ENB,i);
Serial.print(i);
Serial.print("...");
delay(1);
 }
}
```
Przejdźmy teraz do napisania drugiej z funkcji, tym razem odpowiedzialnej za swobodne sterowanie pojazdem. Funkcja będzie przyjmować argumenty odpowiedzialne za stany silników.
```
void freeDrive(int I1, int I2, int I3, int I4){
```
Ustawiamy prędkość na 100%, tak aby mieć jak najwięcej zabawy podczas korzystania z pojazdu w danym trybie.
```
analogWrite(ENA,1024);
analogWrite(ENB,1024);
```
Zapisujemy ustawienia stanów silników i zamykamy drugą z funkcji odpowiedzialnych za sterowanie.
```
digitalWrite(IN1,I1);
digitalWrite(IN2,I2);
digitalWrite(IN3,I4);
digitalWrite(IN4,I4); 
}
```
Następnie piszemy małą funkcję odpowiedzialną za zapisywanie ustawień użytkownika dotyczących prędkości oraz czasu poruszania pojazdu.
```
void setVars(int multi, int t){ 
  multi_ = multi;
  time_ = t;
}
```
Potrzebna będzie jeszcze funkcja z ustawieniami pinów oraz wifi.
```
void setup(){
```
Ustawiamy wcześniej zdefiniowanym pinom tryb wyjścia.
```
pinMode(IN1,OUTPUT); 
pinMode(IN2,OUTPUT); 
pinMode(IN3,OUTPUT); 
pinMode(IN4,OUTPUT); 
pinMode(ENA,OUTPUT); 
pinMode(ENB,OUTPUT);
```
Następnie ustawiamy tryb WiFi jako tryb dostępu (Access Point) i dla pewności wykonujemy rozłączenie z siecią. Tak na wypadek gdyby został wykonany soft reset.
```
WiFi.mode(WIFI_STA); 
WiFi.disconnect();
delay(100);
```
Rozpoczynamy sesje dla serial monitora.
```
Serial.begin(115200); 
Serial.println();
Serial.print("Konfiguracja AP...");
```
Ustawiamy adres ip, bramę domyślną oraz maskę robota i następnie zapisujemy konfigurację sieci. Warto tutaj dodać, że oktety w programie dla adresu ip, bramy oraz maski są oddzielone przecinkiem, a nie kropką tak jak się domyślnie przyjęło.
```
IPAddress ip(192,168,1,200);
IPAddress gateway(192,168,1,254);
IPAddress subnet(255,255,255,0);
WiFi.softAPConfig(ip, gateway, subnet);
```
Następnie włączamy tryb dostępu (Access Point)
```
WiFi.softAP(ssid);
IPAddress myIP = WiFi.softAPIP();
```
oraz pobieramy adres IP i wyświetlamy go w monitorze.
```
Serial.print("AP IP: ");
Serial.println(myIP);
```
Rozpoczynamy sesje serwera TCP.
```
server.begin();
```
Na końcu ustawień dla pewności zatrzymujemy silniki i kończymy funkcję z ustawieniami.
```
digitalWrite(IN1,LOW);
digitalWrite(IN2,LOW); 
digitalWrite(IN3,LOW); 
digitalWrite(IN4,LOW); 
analogWrite(ENA,0);
analogWrite(ENB,0);
}
```
Została ostatnia z funkcji. Mianowicie funkcja odpowiedzialna za sprawdzanie czy klient ( w tym wypadku mata) jest podłączony, odczytywanie komend a następnie ich wykonanie.
```
void loop(){
```
Na początku zapisujemy informacje o połączonym kliencie.
```
WiFiClient client = server.available();
```
Następnie sprawdzamy warunkowo czy zmienna z klientem istnieje oraz czy sam klient jest już podłączony.
```
if (client){
 if(client.connected()){
  Serial.println("Client Connected"); 
 }
```
Tworzymy pętle, która będzie się wykonywać, jeśli klient jest połączony z robotem oraz dopóki liczba połączonych użytkowników będzie większa niż zero.
```
while(client.connected()){
while(client.available()>0){
```
Teraz trzeba odczytać sekwencję znaków przesyłanych przez użytkownika (matę). Sekwencja ta kończyć się będzie znakiem nowej lini.
```
String line = client.readStringUntil('\n');
```
Następnie tworzymy tablice znaków (char), konwertujemy wcześniej odczytaną sekwencję do pojedynczych znaków i zapisujemy je w utworzonej tablicy znaków.
```
char cmd[line.length()+1]; 
line.toCharArray(cmd, line.length()+1);
```
Przechodzimy do pętli, która będzie wykonywała komendy znajdujące się w tablicy.
```
for(int i = 0; i < line.length()+1; i ++){
```
Teraz musimy sprawdzać komendy switchem i następnie wykonać je odpowiednimi case’ami. Każdy przypadek (case) zawiera funkcję "drive" lub “freeDrive”, która zostanie wykonana z argumentami dla konkretnej komendy.
```
switch(cmd[i]){
  case 'u': 
    drive(HIGH, LOW, HIGH, LOW, multi_, time_);
    break;
  case 'd':
    drive(LOW, HIGH, LOW, HIGH, multi_, time_);
    break;
  case 'r':
    drive(LOW, HIGH, HIGH, LOW, multi_, time_);
    break;
  case 'l':
    drive(HIGH, LOW, LOW, HIGH, multi_, time_);
    break;
  case 'z':
    freeDrive(HIGH, LOW, HIGH, LOW);
    break;
  case 'x':
    freeDrive(LOW, HIGH, LOW, HIGH);
    break;
  case 'c':
    freeDrive(LOW, HIGH, HIGH, LOW);
    break;
  case 'v':
    freeDrive(HIGH, LOW, LOW, HIGH);
    break;
```
Na końcu switcha dodajemy jeszcze przypadek, w którym użytkownik podaje nieznane komendy i wykonujemy w niej funkcję drive z argumentami zatrzymującymi pojazd.
```
default:
  drive(LOW,LOW,LOW,LOW,1,0);
  break;
 }
}
```
Odczytujemy jeszcze komendy podane przez serial monitor, gdy aktywna jest jego sesja.
```
while(Serial.available()>0){
   client.write(Serial.read());
  }
 }
}
```
Na koniec zatrzymujemy połączenie z użytkownikiem.
```
client.stop();
  Serial.println("Client disconnected");    
  }
}
```

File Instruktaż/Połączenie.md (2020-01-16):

# 5. **Połączenie robota oraz maty**

## **Opis działania**

W naszym projekcie zdecydowaliśmy, że to robot(Arduino) będzie tworzył sieć wifi i ją konfigurował. Definiujemy port, server,
```
#ifndef PORT 
#define PORT 12345
#endif

WiFiServer server(PORT); 
const char *ssid = APSSID;
```
oraz adres, bramę i maskę sieci.
```
IPAddress ip(192,168,1,200);
IPAddress gateway(192,168,1,254);
IPAddress subnet(255,255,255,0);
WiFi.softAPConfig(ip, gateway, subnet);
WiFi.softAP(ssid);
IPAddress myIP = WiFi.softAPIP(); 
Serial.print("AP IP: ");
Serial.println(myIP);
server.begin();
```
Mata(Raspberry PI) jest w stanie połączyć się z usługą wpisując odpowiedni port oraz adres ip do sieci. 
```
let connected = false
client = new net.Socket();
client.connect(12345, '192.168.1.200', function() {
    console.log('Connected')
  connected = true
})
```
Kiedy wykonamy połączenie, mata będzie w stanie wysłać tekst(string), który zawiera zdefiniowane komendy dla robota. 
```
else if(i == 1) {
    let s = ''
    for(let i in values) {
      for(let j in values[i]) {
        s += values[i][j]
      }
    }
    client.write(s)
    console.log("TCP packet sent: " + s)
  }
```
Robot odpowiednio odczyta dany ciąg komend i wykona instrukcje zgodne z nimi.

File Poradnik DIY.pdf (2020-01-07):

Poradnik „Do It Yourself” do robota sterowanego za pomocą maty.

1. Wstęp.
2. Przygotowanie. (przygotowanie programów, jakiś płytek, lutownicy)
3. Robot.
a) Potrzebne części. (Rozpisać nazwy ze zdjęciami/ewentualne zamienniki/sklepy w których można dostać potrzebne części).
b) Budowa robota od zera z wcześniej przygotowanych części. (jakieś zdjęcia czy filmy instruktażowe)
c) Kod programu do robota.
i. Gotowy do użytku. (Jakiś link do gotowego kodu + opisać do czego służy każda linia kodu)
4. Mata Sterująca.
a) Potrzebne części. (Rozpisać nazwy ze zdjęciami/ewentualne zamienniki/sklepy w których można dostać potrzebne części).
b) Budowa maty od zera z wcześniej przygotowanych części. (jakieś zdjęcia czy filmy instruktażowe)
c) Kod programu do maty.
i. Gotowy do użytku. (Jakiś link do gotowego kodu + opisać do czego służy każda linia kodu)
5. Połączenie robota z matą za pomocą programu.
a) Gotowy do użytku. (Jakiś link do gotowego kodu + opisać do czego służy każda linia kodu)
6. Podsumowanie.
a) Sugestie dla użytkownika. (np. dorzucenie czujników)

1. Wstęp.

Cześć, jesteśmy grupą studentów, którzy na swój projekt inżynierski postanowili stworzyć niedużego robota sterowanego za pomocą interaktywnej maty.

Robot sterowany jest za pomocą sekwencji, które wprowadzamy na w/w macie. Możemy dawać mu proste komendy pozwalające na poruszanie się. Alternatywnym trybem jest jazda swobodna pozwalająca na sterowanie robotem w czasie rzeczywistym.

Mata jest urządzeniem posiadającym układ przycisków 4x4 i ekran pokazujący aktualnie wpisywaną sekwencję.

Posiadając podstawową wiedzę na temat programowania i elektroniki, będziesz mógł skonstruować taki zestaw sam, w zaciszu swojego domu. Zalecamy z zapoznaniem się dokładnie z poradnikiem przed próbą konstrukcji. Powodzenia!

2. Przygotowanie.

Do utworzenia naszego projektu, będą potrzebne:

NodeMCU(Arduino)

ESP8266 jest popularnym mikrokontrolerem z wbudowanym WiFi. Dzięki atrakcyjnej cenie i dużym możliwościom stał się bardzo popularny, zwłaszcza w zakresie automatyki domowej.

Moduł NodeMCU to Arduino z wlutowanym ESP8266-12. Arduino pozwala nam sterować pozostałymi częściami elektronicznymi w projekcie a ESP zapewnia nam bezprzewodową łączność.

W naszym projekcie mikrokontroler będzie wykorzystany do sterowania robotem oraz do tworzenia sieci WiFi, do której będzie łączyć się nasza mata.

Arduino IDE

Natomiast do napisania odpowiedniego oprogramowania przyda nam się Arduino IDE, które pozwala zaprogramować nam NodeMCU językiem C. Do poprawnego działania IDE z NodeMCU potrzebne są dodatkowe biblioteki co opiszemy w dalszej części poradnika.

Program ten jest w pełni darmowy i można go uruchomić na Windowsie, Linuxie lub Mac-Osie. Dostępny jest na przykład tutaj:

https://www.arduino.cc/en/Main/Software


Wciskamy interesujący nas link z installerem z prawej strony i przechodzimy dalej. Ja wykorzystam tutaj instalator dla systemu Windows.


Jak wspomniałem, program jest w pełni darmowy dlatego strona proponuje nam dobrowolny podarunek pieniężny, więc jeżeli czujesz że chcesz wspomóc twórców - śmiało zaznacz interesującą Cię kwotę i przejdź dalej przyciskiem “CONTRIBUTE & DOWNLOAD”. Ja natomiast przejdę do pobierania wciskając przycisk “JUST DOWNLOAD”.

Czekamy aż instalka skończy się pobierać i przechodzimy do instalacji programu. Oczywiście czytamy całą umowę licencyjną i jeśli nie mamy zastrzeżeń wciskamy “I Agree”.


Wybieramy zawartość, którą chcemy zainstalować i przechodzimy dalej.

Następnie wybieramy folder, do którego chcemy zainstalować nasze IDE.


Po zakończonej instalacji zamykamy installer i nasze IDE jest już prawie gotowe do użytku. Musimy je jeszcze odpowiednio skonfigurować.

Konfiguracja IDE

Zaczynamy od włączenia IDE, jeśli zostało przez nas wyłączone. Następnie otwieramy menu preferencji.


Kopiujemy podaną linie i wklejamy do pola “Dodatkowe adresy URL do menedżera płytek” http://arduino.esp8266.com/stable/package_esp8266com_index.json i potwierdzamy przyciskiem OK.

Kolejnym krokiem jest przejście do menedżera płytek.

W polu wyszukiwania wpisujemy “esp8266” a następnie instalujemy dany pakiet.

Po zakończonej instalacji pakietu, zamykamy okno menedżera płytek i klikamy jeszcze raz w narzędzia i wybieramy “Generic ESP8266 Module” z listy dostępnych płytek.


Kiedy już wybierzemy odpowiedni moduł płytki nasze IDE jest w pełni skonfigurowane i gotowe do użytku.

Raspberry Pi Zero

Minikomputer Raspberry Pi w wersji miniaturowej. Wyposażony w procesor Broadcom BCM2835 1 GHz i 512 MB pamięci RAM, WiFi, Bluetooth, port miniHDMI, gniazdo microUSB OTG, 40 GPIO, złącza na kartę microSD oraz cztery otwory montażowe. Wymiary płytki to: 65 x 30 x 5 mm. Ta wersja posiada wlutowane złącza męskie GPIO.

Nasza “malinka” będzie odpowiedzialna za sterowanie matą.

Przykładowy link do sklepu:

https://botland.com.pl/pl/moduly-i-zestawy-raspberry-pi-zero/9749-raspberry-pi-zero-wh-5 12mb-ram-wifi-bt-41-ze-zlaczami.html (https://botland.com.pl/pl/moduly-i-zestawy-raspberry-pi-zero/9749-raspberry-pi-zero-wh-512mb-ram-wifi-bt-41-ze-zlaczami.html)

Niestety, w chwili pisania poradnika, malinka dostępna jest tylko na botlandzie lub allegro.

Części do budowy robota oraz maty

Oczywiście do budowy naszego projektu będą potrzebne różne części, które opiszemy w kolejnych rozdziałach.

Płytki PCB


Zdjęcie przedstawia schemat połączeń w macie. Przyciski, ekran oraz konektor do Raspberry Pi

Zdjęcie przedstawia projekt płytki drukowanej dwustronnej. Czerwone linie oznaczają ścieżki na górnej warstwie laminatu, niebieskie na dolnej warstwie.
Do naszego robota oraz maty będzie potrzeba po jednej płytce pcb. W tym miejscu mamy dwa sposoby na ich przygotowanie. Możesz je przygotować samemu, tak jak zrobiliśmy to my lub możesz takowe płytki zamówić za dodatkową opłatą. Jeśli zdecydujesz się zamówić płytki, będzie Ci potrzebny jedynie plik ze schematem, który musisz wysłać do odpowiedniej firmy.

tu wstaw plik ze schematem - schematy gotowe, wrzucić na gita i podlinkować

Przykładowe linki do firm:

1. https://jlcpcb.com/ - czas wykonania, około 3 tygodnie
2. https://www.pcbway.com/ - czas wykonania zależy od obliczenia, mniej więcej 1,5 tygodnia
3. https://www.fabrykapcb.pl/index.html - czas wykonania, około tygodnia

Przejdźmy teraz do przygotowania płytek w warunkach domowych.

Przygotowanie

Potrzebne Ci będzie kilka rzeczy,

- płyta grzejna lub żelazko, najlepiej takie bez dziurek z płaską powierzchnią, inaczej płytka może się wygiąć,
- projekt PCB, który dostaniesz od nas

- najistotniejsza będzie jednak drukarka laserowa, jeśli jednak nie masz, popytaj znajomych, w punktach ksero najczęściej odmawiają - jest ryzyko przyklejenia się papieru do głowicy,
- cienki papier kredowy
https://www.ebiuromax.pl/papier-kredowy-a4-135g-50-blyszczacy.htmlhttps://biurwa.pl/papier-kredowy-kreska-a4-130g
- mała wiertarka modelarska, najlepiej z tytanowymi wiertłami o szerokości 1mm, https://botland.com.pl/pl/wiertarki-i-wkretarki/665-miniwiertarka-velleman-vthd01-z-akcesoriami-5410329377823.html (https://botland.com.pl/pl/wiertarki-i-wkretarki/665-miniwiertarka-velleman-vthd01-z-akcesoriami-5410329377823.html) https://abc-rc.pl/product-pol-7932-Mini-Wiertarka-modelarska-Szlifierka-12V-Vellem an-VTHD01.html (https://abc-rc.pl/product-pol-7932-Mini-Wiertarka-modelarska-Szlifierka-12V-Velleman-VTHD01.html)
- kwas b327 (nadsiarczan sodowy), https://botland.com.pl/pl/wytrawiacze/1057-wytrawiacz-b327-100g-5901764329183 .html (https://botland.com.pl/pl/wytrawiacze/1057-wytrawiacz-b327-100g-5901764329183.html)
https://abc-rc.pl/product-pol-10124-Wytrawiacz-do-plytek-drukowanych-B327-Nadsi arczan-sodowy.html (https://abc-rc.pl/product-pol-10124-Wytrawiacz-do-plytek-drukowanych-B327-Nadsiarczan-sodowy.html)
- aceton,
https://www.ichemia.pl/37,aceton-99-9-hybrydy-250-ml.html
aceton możemy kupić spokojnie na allegro - nie ma zbyt dużego wyboru, potrzebujemy czysty aceton, w niedużej ilości, wystarczy nawet 100ml.
Zamiast acetonu możemy użyć IPA - alkohol izopropylowy. https://botland.com.pl/pl/smary-i-oczyszczacze/974-kontakt-ipa-plus-oliwiarka-100m l-5901764329930.html (https://botland.com.pl/pl/smary-i-oczyszczacze/974-kontakt-ipa-plus-oliwiarka-100ml-5901764329930.html)
https://abc-rc.pl/product-pol-9033-Izopropanol-AG-Kontakt-IPA-plus-100ml.html Ostatecznie możemy użyć zmywacza do paznokci zawierającego aceton. Dzisiaj często zmywacze są z odżywkami i zawierają jedynie śladowe ilości acetonu, ale jeśli znajdziemy/mamy dostęp do takiego bez odżywek, będzie wystarczająco dobry do wyczyszczenia płytki.
- miedziane tulejki 0.9mm, https://www.gotronik.pl/tulejki-miedziane-0-90mm-do-wykonywania-przelotek-p-49 45.html (https://www.gotronik.pl/tulejki-miedziane-0-90mm-do-wykonywania-przelotek-p-4945.html)
tulejki możemy również kupić na allegro - trzeba jedynie pamiętać aby były miedziane o średnicy 0.9mm
- przyda się również gąbka druciana lub papier ścierny o gradacji (ziarnistości) większej niż 600
https://www.castorama.pl/papier-wodoodporny-condor-230-x-280-mm-gradacja-80 0-id-85959.html (https://www.castorama.pl/papier-wodoodporny-condor-230-x-280-mm-gradacja-800-id-85959.html)
https://www.leroymerlin.pl/narzedzia-reczne/materialy-scierne-szczotki-druciane/materialy-scierne-ciete-i-w-arkuszach/papier-scierny-wodny-p800-230-x-280-mm-dext er,p453983,l810.html (https://www.leroymerlin.pl/narzedzia-reczne/materialy-scierne-szczotki-druciane/materialy-scierne-ciete-i-w-arkuszach/papier-scierny-wodny-p800-230-x-280-mm-d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)
- marker permamentny,
https://botland.com.pl/pl/markery/952-marker-permanentny-czarny-pentel-n850-49 02506071361.html (https://botland.com.pl/pl/markery/952-marker-permanentny-czarny-pentel-n850-4902506071361.html)
https://abc-rc.pl/product-pol-9594-Marker-do-rysowania-sciezek-0-3mm-czarny.html

- gumowe rękawiczki - kwas, który będziemy używać nie jest groźny przy kontakcie ze skórą. Nie zmienia to faktu, że lepiej zachować ostrożność.

Zanim przejdziesz już do tworzenia płytki, pamiętaj aby zachować wszelką ostrożność! Powinieneś znajdować się w dobrze wentylowanym pomieszczeniu.

Drukowanie

W tym kroku jest nam potrzebna drukarka laserowa. Jak wspomniałem wyżej, jeśli masz -świetnie, jeśli jednak nie, popytaj znajomych. Musimy wydrukować schemat płytki, najlepiej żebyś to zrobił przy użyciu papieru kredowego - jest tani i łatwo dostępny, także nie powinieneś mieć problemu z dostaniem go.


Wymiarowanie

Teraz przykładamy schemat do płytki i wiercimy dziurki w rogach schematu na płytce, tak aby góra i dół pokrywały się ze sobą, ponieważ płytka będzie dwustronna. Następnie docinamy płytkę do wielkości schematu i przechodzimy do kolejnego kroku.


Czyszczenie powierzchni

Powierzchnię płytki należy oczyścić przed wykonaniem kolejnych czynności. Odbywa się to w dwóch krokach. Najpierw szlifujemy lekko powierzchnię z obu stron płytki używając papieru ściernego lub druciaka. Po zakończonym procesie szlifowania przecieramy powierzchnię alkoholem bądź acetonem - my użyliśmy do tego starej szczoteczki do zębów maczanej w czystym acetonie.

Nakładanie ścieżek

Zaczynamy od rozgrzania żelazka, musi być ustawione na maksymalną temperaturę. Przyda się tutaj jakaś płaska powierzchnia jak na przykład kafelki w łazience czy kuchni albo drewniana deska do krojenia. Układamy kawałek papieru ręcznikowego lub toaletowego. Na papierze układamy płytkę, tak aby nie dotykała kafelek. Następnie na płytkę kładziemy papier kredowy z wydrukowanym schematem i ustawiamy zgodnie z wyrobionymi dziurkami. Toner
powinien być ustawiony do dołu.
Dokładamy kolejny kawałek papieru

ręcznikowego, uważając żeby schemat na płytce nie przesunął się. Kiedy już wszystko jest ładnie ustawione, dociskamy całość rozgrzanym żelazkiem i co kilka sekund wykonujemy ruch prasowania. Cały proces powinien trwać około 5 minut.

Po zakończonym procesie
nakładania, ostrożnie wyciągamy płytkę (powinieneś tu zachować ostrożność, całość może być dosyć gorąca). Następnie płytkę z przyklejonym już schematem ostrożnie odkładamy w misce i chłodzimy pod bieżącą wodą, przy okazji warto namoczyć przyklejony schemat.
Kiedy schemat będzie już dobrze namoczony, powoli odrywamy go od płytki. Na naszej płytce powinien


być obecnie widoczny toner ze ścieżkami, jeżeli dostrzegasz jakieś przerwane ścieżki, możesz je ostrożnie poprawić markerem permamentnym.

Cały proces powtarzamy dla drugiej strony laminatu. Wywiercone wcześniej dziury pozwolą ułożyć wydruk tak, aby pokrywał się z drugą stroną.

Wiercenie

Musimy teraz wywiercić małe otwory na piny. Używamy do tego naszej wiertarki modelarskiej z tytanowym wiertłem o szerokości 1mm. Następnie w powstałe otwory wbijamy miedziane tulejki.

~~przyda się jakieś zdjęcie~~

Wytrawianie
W tym miejscu powinieneś założyć swoje gumowe rękawiczki. Sam roztwór nie powinien być niebezpieczny, jednak ostrożności nigdy za wiele!

Przejdziemy teraz do utworzenia roztworu, który wytrawi miedź z płytki. Przygotuj 100 gramów kwasu B327 oraz pół litra wody (takie są proporcje roztworu), najlepiej o temperaturze 50 stopni, jeżeli nie jesteś w stanie kontrolować temperatury wody możesz ostatecznie użyć wrzątku. Zalewasz kwas ciepłą wodą i mieszasz wszystko do momentu, w którym kryształki kwasu się rozpuszczą.

Do utworzonego roztworu wrzucamy naszą płytkę. Całość najlepiej umieścić w płaskim pudełku. Kiedy płytka znajduje się w środku, potrząsaj lekko pudełkiem, tak aby mieszanka była cały czas w ruchu, ponieważ to przyspiesza proces trawienia. Całość powinna trwać od 5 do 10 minut. Po upływie około 3 minut, obróć płytkę, aby zobaczyć jak proces trawienia przebiega z drugiej strony.

Kiedy miedź zostanie usunięta z miejsc, w których nie ma toneru, proces trawienia można uznać za zakończony. Wyciągamy płytkę z mieszanki. Następnie płytkę wycieramy i myjemy pod bieżącą wodą.

Warto tutaj dodać, że jeśli planujesz zrobić więcej płytek, to roztwór jest wielokrotnego użytku, jednak z każdym użyciem będzie zmieniał kolor na coraz bardziej niebieski i proces trawienia będzie odrobinę wolniejszy.

Sprawdzamy teraz czy wszystkie ścieżki wyglądają poprawnie, jeśli tak to zmywamy toner acetonem. Miejsca, w których toner przykleił się bardzo mocno, można lekko przetrzeć papierem ściernym lub drucianą gąbką.

Pistolet do kleju


Zalecane właściwości:

- Moc - 10 W,
- Średnica kleju - 8 mm,

Przykładowy link:

https://abc-rc.pl/product-pol-11945-Pistolet-do-kleju-na-goraco-110-240V-40W-Glue-Gun.ht ml (https://abc-rc.pl/product-pol-11945-Pistolet-do-kleju-na-goraco-110-240V-40W-Glue-Gun.html) +
https://abc-rc.pl/product-pol-11946-Klej-do-pistoletu-na-goraco-16x1-1cm-klej-do-klejenia-n a-goraco-przezroczysty.html (https://abc-rc.pl/product-pol-11946-Klej-do-pistoletu-na-goraco-16x1-1cm-klej-do-klejenia-na-goraco-przezroczysty.html)

https://botland.com.pl/pl/kleje-i-klejarki/976-pistolet-do-klejenia-20w-zd-5.htmlhttps://botland.com.pl/pl/kleje-i-klejarki/896-klej-do-pistoletu-cienki-74150-mm-prz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 sty.htmlv (https://botland.com.pl/pl/kleje-i-klejarki/896-klej-do-pistoletu-cienki-74150-mm-przezroczysty.htmlv)

Lutownica kolbowa

Zalecane właściwości:

- Napięcie zasilania - 230 V,
- Moc - 60 W,

Przykładowy link do sklepu:

https://botland.com.pl/pl/lutownice-kolbowe/1126-lutownica-kolbowa-zd200c-oporowa-60 w.html (https://botland.com.pl/pl/lutownice-kolbowe/1126-lutownica-kolbowa-zd200c-oporowa-60w.html)

https://abc-rc.pl/product-pol-12145-Lutownica-220V-60W-regulacja-temperatury.html

Śrubokręt i śrubki

- śrubokręt płaski 3.0
https://botland.com.pl/pl/wkretaki-i-klucze/635-zestaw-wkretakow-plaskich-mini-6s zt.html (https://botland.com.pl/pl/wkretaki-i-klucze/635-zestaw-wkretakow-plaskich-mini-6szt.html)
- śrubokręt krzyżakowy PH1
- 4 śrubki M3x12mm
- 4 nakrętki M3
https://botland.com.pl/pl/srubki-i-nakretki/636-zestaw-srubki-i-nakretki-180szt-5410 329304485.html (https://botland.com.pl/pl/srubki-i-nakretki/636-zestaw-srubki-i-nakretki-180szt-5410329304485.html)
3. Robot.


Lista wymaganych materiałów.

1) Chassis Rectangle 2WD 2-kołowe podwozie robota z napędem – 1 sztuka

Przezroczysta platforma do budowy robota. W zestawie znajdują się dwa silniki prądu stałego z kołami o średnicy 65 mm. W części przedniej podporę stanowi metalowe koło obrotowe. Elementy podwozia są zrobione z akrylu, posiadają otwory montażowe pozwalające zamontować różnego rodzaju sensory czy kontrolery.

Zestaw zawiera:

- Platformę montażową
- Dwa koła z oponami o średnicy 65 mm
- Dwa silniki prądu stałego z przekładniami
- Jedno metalowe koło obrotowe montowane przy pomocy dwóch śrub
- Metalowe oraz plastikowe podzespoły (śrubki, nakrętki, itp.)
- Włącznik
- Koszyk na baterie (4 x AA) ze przewodami ze zdjętą izolacją

Warto tutaj dodać, że jeśli zdecydujesz się na zakup danego podwozia, to nie musisz już martwić się o silniki oraz koła, ponieważ są zawarte w tym zestawie. Natomiast nadal powinieneś zakupić podany w tej liście koszyk na baterie.

Przykładowy link do sklepu:

https://botland.com.pl/pl/podwozia-robotow/7283-chassis-rectangle-2wd-2-kolowe-podwozie-robota-z-napedem.html (https://botland.com.pl/pl/podwozia-robotow/7283-chassis-rectangle-2wd-2-kolowe-podwozie-robota-z-napedem.html)

https://abc-rc.pl/product-pol-7656-Podwozie-robota-2WD-RT-5-210mm-2-silniki-pod wozie-Arduino.html (https://abc-rc.pl/product-pol-7656-Podwozie-robota-2WD-RT-5-210mm-2-silniki-podwozie-Arduino.html)

2) Silnik DC z przekładnią 1:48 – 2 sztuki (zawarte w zestawie z podwoziem)

Unikalna jednostka napędowa do Twojego robota. Silnik prądu stałego z przekładnią 1:48 zapewni wspaniałe osiągi dla Twojego robota. Dwustronna oś pozwala zamontować koło z oponą z dowolnej strony.

3) Koło plastikowe z oponą 65/25 mm – 2 sztuki (zawarte w zestawie z podwoziem)

Doskonała ochrona przed aquaplaningiem. Krótka droga hamowania. Bardzo dobra przyczepność na zakrętach. Niski poziom hałasu przez cały okres eksploatacji opony.

4) Moduł dwukanałowego sterownika silników z L298N – 1 sztuka

Umożliwia on sterowanie jednocześnie dwóch silników DC lub jednego silnika krokowego. Kontroler ten pozwala ustawić stałą (pełną) prędkość obrotu kół, lub kontrolować ją sygnałem PWM.

Przykładowy link do sklepu:

https://abc-rc.pl/product-pol-6196-Modul-sterownika-L298N-do-silnikow-DC-i-kroko wych-Arduino.html (https://abc-rc.pl/product-pol-6196-Modul-sterownika-L298N-do-silnikow-DC-i-krokowych-Arduino.html)

https://nettigo.pl/products/modul-dwukanalowego-sterownika-silnikow-z-l298n

5) Moduł WiFi NodeMCU V3 LoLin ESP-12E(Arduino) – 1 sztuka

Przykładowy link do sklepu:

https://nettigo.pl/products/modul-wifi-nodemcu-v3-lolin-esp-12e

6) Zestaw rezystorów i kondensatorów – (100mikrofaradów, 16v)

LINK DO POJEDYNCZEJ SZTUKI

Przykładowy link do sklepu:

https://nettigo.pl/products/zestaw-rezystorow-i-kondensatorow--2

7) Dwupozycyjny przełącznik MTS-102 – 1 sztuka

Przełącznik dźwigniowy, dwupozycyjny, jednosekcyjny, MTS-1.

Dane techniczne:

Rodzaj napięcia AC/DC Obciążenie do 3A przy 250V Obciążenie do 6A przy 125V Wysokość: 33mm Średnica otworu montażowego: 6mm

Przykładowy link do sklepu:

https://nettigo.pl/products/dwupozycyjny-przelacznik-mts-102

8) Koszyk na dwa ogniwa 18650 2S z wtykiem 2.1x5.5 – 1 sztuka

Łączy w szereg dwa ogniwa 18650. Daje to od ~7.0 do 8.4 V w zależności od naładowania ogniw. Długi 30-centymetrowy kabel daje się ładnie układać.

Przykładowy link do sklepu:

https://nettigo.pl/products/koszyk-na-dwa-ogniwa-18650-2s-z-wtykiem-2-1x5-5

9) Stabilizator liniowy 3.3V 0.8A – 1 sztuka

Przykładowy link do sklepu:

https://nettigo.pl/products/stabilizator-liniowy-3-3v-0-8a

Budowa Robota

Będąc odpowiednio przygotowanym, możemy przejść do budowy naszego robota.

Przygotowanie silników

Sprawdzamy czy w silnikach mamy zlutowane kabelki, jeśli są to przejdź do kroku.

Zdejmujemy najpierw mały kawałek izolacji na kabelkach - około 1 do 2mm, możesz do tego użyć na przykład noża do tapet. Lekko natnij izolację i pociągnij, powinna bez problemu zejść.

Następnie potrzebujemy rozgrzać lutownicę, jeżeli posiadasz zwykłą kolbową - dotknij grotu cyną, jeśli będzie się topić to lutownica jest wystarczająco nagrzana, jeśli jednak posiadasz lutownicę z możliwością regulacji temperatury - ustaw ją w okolicach 400-450 stopni.

Odsłonięty kabel przykładamy do dziurki w blaszce silnika - kolor kabelka jest obecnie nieistotny, polaryzację możemy zmienić później w kodzie robota. Przykładamy rozgrzaną lutownicę do odsłoniętego kabelka i nakładamy cynę tak, aby pokryła kabelek razem z blaszką nie zostawiając dziur. Oczywiście nie powinieneś ruszać kabelkiem w trakcie lutowania. Po krótkiej chwili lut zastygnie i połączenie będzie gotowe. Powtarzamy tą czynność dla reszty kabelków.


Jeśli korzystasz z koszyka na ogniwa, które podaliśmy w liście części, prawdopodobnie nie będzie musiał lutować kabelków. Jeśli jednak koszyk nie miałby kabli lub miałbyś inny koszyk na baterie, powtórz powyższe czynności.

Lutowanie włącznika

Istotnym jest jeszcze dolutowanie przycisku włączenia/wyłączenia, bez tego nasz robot się nie uruchomi. Łapiemy za koszyk na ogniwo i ucinamy czarny kabelek mniej więcej w połowie.

Teraz musimy jeszcze zdjąć kawałek izolacji na końcu kabelka od koszyka oraz z obu stron na uciętym kawałku kabelka.


Następnie przechodzimy do lutowania. Kabelek, który został odcięty lutujemy do blaszki w miejscu, w którym znajduje się “I” na przycisku, a w miejscu “O” powinniśmy dolutować czarny kabel, który wychodzi od koszyka na ogniwa. “I” oznacza włączony, a “O” wyłączony.

Lutowanie płytki

~~DODAĆ OPIS~~

Po zakończonym lutowaniu dobrze jest wgrać kod do robota, tak dla wygody. Opis jak to zrobić znajdziesz w kolejnym dziale nazwanym “Kod do robota”.

Przygotowanie podwozia


Musimy odpowiednio wywiercić otwory w podwoziu, tak aby móc zamontować części w odpowiednich miejscach. Przykładamy koszyki od akumulatorów i zaznaczamy markerem miejsca, w których następnie wiercimy otwory.

Do wiercenia używamy wiertła 3mm.

Czynności powtarzamy dla płytki od Node’a oraz kontrolera DC.


Na koniec odklejamy jeszcze folię zabezpieczającą podwozie.

Montaż części


Łapiemy za śrubokręt krzyżakowy oraz śrubki ~~OPISAĆ DOKŁADNIEJ JAKIE~~ i przykręcamy do podwozia części, dla których wywierciliśmy otwory w punkcie powyżej.

Następnie montujemy silniki w uchwytach montażowych.


Przykręcamy również koło obrotowe, dla którego zrobiono miejsca na przodzie podwozia.


Po zamontowaniu wszystkich części, polecamy użyć pistoletu na klej i zakleić koło obrotowe. Dzięki temu, robot będzie bardziej stabilny podczas jazdy. Uważaj tylko żeby przyklejone koło było ustawione prosto, inaczej robot będzie niepotrzebnie skręcał w trakcie jazdy.

Połączenie części

Zaczynamy od połączenia kabli silników do wejść na kontrolerze DC - są to skręcane, skrajne podwójne wejścia. Następnie lutujemy kable odpowiedzialne za zasilanie do płytki od Node’a. Łączymy jeszcze zasilanie Node’a z kontrolerem DC - plus do wejścia 12V a minus do wejścia GND. Na koniec łączymy piny od płytki z pinami kontrolera. ~~OPISAĆ DOKŁADNIEJ KTÓRE GDZIE~~

Kod do robota

Cały kod, gotowy do wklejenia i przerzucenia do robota znajdziesz pod tym linkiem:

~~TU LINK DO KODU~~

Pobierz plik z kodem i otwórz go we wspomnianym wcześniej Arduino IDE. Następnie podłącz robota do swojego komputera. Mając otwarty plik z kodem w IDE oraz podłączonego robota, wciśnij ikonę strzałki w programie i poczekaj aż kod zostanie wgrany do robota.

A jeśli interesuje Cię co się w tym kodzie znajduje, poniżej opiszę kod krok po kroku.

Zacznijmy od dołączenia odpowiedniej biblioteki, która odpowiedzialna będzie za obsługę ESP8266.

#include <ESP8266WiFi.h>

Następnie definiujemy nazwę sieci, jeśli zmienna APSSID, w której umieszczamy nazwę naszej sieci nie jest zdefiniowana, to deklarujemy ją warunkowo.

#ifndef APSSID

#define APSSID "Robot"

#endif

I powtarzamy czynność dla zmiennej PORT.

#ifndef PORT

#define PORT 12345

#endif

Przechodzimy do zdefiniowania zmiennej odpowiedzialnej za przechowywanie serwera.

WiFiServer server(PORT);
const char *ssid = APSSID;
Na koniec definiujemy zmienne odpowiadające za piny do silników, prędkość, czas jazdy pojazdu i diodę LED.

int IN1=12;

int IN2=14;
int IN3=4;
int IN4=5;
int ENA=0;
int ENB=13;
int multi_=1;
int time_=250;
int led=2;
Musimy teraz napisać funkcje odpowiedzialne za sterowanie robotem w obu trybach, więc przejdziemy do napisania pierwszej z funkcji odpowiedzialnej za sterowanie robotem. Funkcja będzie przyjmować argumenty odpowiedzialne za stany silników, mnożnik prędkości oraz czas poruszania.

void drive(int I1, int I2, int I3, int I4, int multi, int t){ Następnie zapisujemy ustawienia stanów silników.

digitalWrite(IN1,I1);
digitalWrite(IN2,I2);
digitalWrite(IN3,I3);
digitalWrite(IN4,I4);
I przechodzimy do napisania pętli odpowiedzialnej za płynne rozpędzanie naszego pojazdu.

Serial.println("Akceleracja:");
for(int i = 0; i < 1024; i += multi){
Ustawiamy prędkości silników.

analogWrite(ENA,i);
analogWrite(ENB,i);
Serial.print(i);
Serial.print("...");
delay(1);
}
Skoro już rozpędziliśmy naszego robota, musimy teraz napisać pętlę odpowiedzialną za jego płynne hamowanie.

delay(t);
Serial.println("Hamowanie:");
for(int i = 1024; i > 0; i -= multi){
Tak jak przy rozpędzaniu, ustawiamy prędkości silników również przy hamowaniu i kończymy jedną z funkcji odpowiedzialną za sterowanie.

analogWrite(ENA,i);
analogWrite(ENB,i);
Serial.print(i);
Serial.print("...");
delay(1);
}
}
Przejdźmy teraz do napisania drugiej z funkcji, tym razem odpowiedzialnej za swobodne sterowanie pojazdem. Funkcja będzie przyjmować argumenty odpowiedzialne za stany silników.

void freeDrive(int I1, int I2, int I3, int I4){
Ustawiamy prędkość na 100%, tak aby mieć jak najwięcej zabawy podczas korzystania z pojazdu w danym trybie.

analogWrite(ENA,1024);
analogWrite(ENB,1024);
Zapisujemy ustawienia stanów silników i zamykamy drugą z funkcji odpowiedzialnych za sterowanie.

digitalWrite(IN1,I1);
digitalWrite(IN2,I2);
digitalWrite(IN3,I4);
digitalWrite(IN4,I4);
}
Następnie piszemy małą funkcję odpowiedzialną za zapisywanie ustawień użytkownika dotyczących prędkości oraz czasu poruszania pojazdu.

void setVars(int multi, int t){
multi_ = multi;
time_ = t;
}
Potrzebna będzie jeszcze funkcja z ustawieniami pinów oraz wifi.

void setup(){
Ustawiamy wcześniej zdefiniowanym pinom tryb wyjścia.

pinMode(IN1,OUTPUT);
pinMode(IN2,OUTPUT);
pinMode(IN3,OUTPUT);
pinMode(IN4,OUTPUT);
pinMode(ENA,OUTPUT);
pinMode(ENB,OUTPUT);
Następnie ustawiamy tryb WiFi jako tryb dostępu (Access Point) i dla pewności wykonujemy rozłączenie z siecią. Tak na wypadek gdyby został wykonany soft reset.

WiFi.mode(WIFI_STA);
WiFi.disconnect();
delay(100);
Rozpoczynamy sesje dla serial monitora.

Serial.begin(115200);
Serial.println();
Serial.print("Konfiguracja AP...");
Ustawiamy adres ip, bramę domyślną oraz maskę robota i następnie zapisujemy konfigurację sieci. Warto tutaj dodać, że oktety w programie dla adresu ip, bramy oraz maski są oddzielone przecinkiem, a nie kropką tak jak się domyślnie przyjęło.

IPAddress ip(192,168,1,200);
IPAddress gateway(192,168,1,254);
IPAddress subnet(255,255,255,0);
WiFi.softAPConfig(ip, gateway, subnet); Następnie włączamy tryb dostępu (Access Point)

WiFi.softAP(ssid);
IPAddress myIP = WiFi.softAPIP();

oraz pobieramy adres IP i wyświetlamy go w monitorze.

Serial.print("AP IP: ");
Serial.println(myIP);
Rozpoczynamy sesje serwera TCP.

server.begin();
Na końcu ustawień dla pewności zatrzymujemy silniki i kończymy funkcję z ustawieniami.

digitalWrite(IN1,LOW);
digitalWrite(IN2,LOW);
digitalWrite(IN3,LOW);
digitalWrite(IN4,LOW);
analogWrite(ENA,0);
analogWrite(ENB,0);
}
Została ostatnia z funkcji. Mianowicie funkcja odpowiedzialna za sprawdzanie czy klient ( w tym wypadku mata) jest podłączony, odczytywanie komend a następnie ich wykonanie.

void loop(){
Na początku zapisujemy informacje o połączonym kliencie.

WiFiClient client = server.available();
Następnie sprawdzamy warunkowo czy zmienna z klientem istnieje oraz czy sam klient jest już podłączony.

if (client){
if(client.connected()){
Serial.println("Client Connected");
}
Tworzymy pętle, która będzie się wykonywać, jeśli klient jest połączony z robotem oraz dopóki liczba połączonych użytkowników będzie większa niż zero.

while(client.connected()){
while(client.available()>0){
Teraz trzeba odczytać sekwencję znaków przesyłanych przez użytkownika (matę). Sekwencja ta kończyć się będzie znakiem nowej lini.

String line = client.readStringUntil('\n');
Następnie tworzymy tablice znaków (char), konwertujemy wcześniej odczytaną sekwencję do pojedynczych znaków i zapisujemy je w utworzonej tablicy znaków.

char cmd[line.length()+1];
line.toCharArray(cmd, line.length()+1);
Teraz przechodzimy do pętli, która będzie wykonywała komendy znajdujące się w tablicy.

for(int i = 0; i < line.length()+1; i ++){
Teraz musimy sprawdzać komendy switchem i następnie wykonać je odpowiednimi case’ami. Każdy przypadek (case) zawiera funkcję “drive” lub “freeDrive”, która zostanie wykonana z argumentami dla konkretnej komendy.

switch(cmd[i]){
case 'u':
drive(HIGH, LOW, HIGH, LOW, multi_, time_); break;

case 'd':
drive(LOW, HIGH, LOW, HIGH, multi_, time_); break;
case 'r':
drive(LOW, HIGH, HIGH, LOW, multi_, time_); break;
case 'l':
drive(HIGH, LOW, LOW, HIGH, multi_, time_); break;
case 'z':
freeDrive(HIGH, LOW, HIGH, LOW);
break;
case 'x':
freeDrive(LOW, HIGH, LOW, HIGH); break;
case 'c':
freeDrive(LOW, HIGH, HIGH, LOW); break;
case 'v':
freeDrive(HIGH, LOW, LOW, HIGH);
break;
Na końcu switcha dodajemy jeszcze przypadek, w którym użytkownik podaje nieznane komendy i wykonujemy w niej funkcję drive z argumentami zatrzymującymi pojazd.

default:
drive(LOW,LOW,LOW,LOW,1,0);
break;
}
}
Odczytujemy jeszcze komendy podane przez serial monitor, gdy aktywna jest jego sesja.

while(Serial.available()>0){
client.write(Serial.read());
}
}
}
Na koniec zatrzymujemy połączenie z użytkownikiem.

client.stop();
Serial.println("Client disconnected"); }
}

## 4. Mata sterująca

## ( tu wstawić zdjęcie maty )

Lista wymaganych materiałów:

1) RPi Zero + piny (wychodzi taniej)

Przykładowy link do sklepu:

https://botland.com.pl/pl/moduly-i-zestawy-raspberry-pi-zero/8330-raspberry-pi-zero-w-512mb-ram-wifi-bt-41.html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 (https://botland.com.pl/pl/moduly-i-zestawy-raspberry-pi-zero/8330-raspberry-pi-zero-w-512mb-ram-wifi-bt-41.html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)

https://botland.com.pl/pl/gniazda-szpilkowe-goldpin/12659-wtyk-goldpin-2x20-prosty-raster-254m m.html (https://botland.com.pl/pl/gniazda-szpilkowe-goldpin/12659-wtyk-goldpin-2x20-prosty-raster-254mm.html)

2) Płytka uniwersalna:


Przykładowy link do sklepu:

https://allegro.pl/kategoria/plytki-drukowane-moduly-plytki-uniwersalne-67365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 (https://allegro.pl/kategoria/plytki-drukowane-moduly-plytki-uniwersalne-67365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)

Wymiary minimalne: 9cm x 15cm

Komentarz: + dodatkowa 2cm x 8cm do budowy płytki zasilającej

3) Części do płytki drukowanej:

Przykładowy link do sklepu:

https://botland.com.pl/pl/laminaty/1054-laminat-fr4-dwustronny-rozmiar-l.htmlhttps://botland.com.pl/pl/laminaty/1943-laminat-dwustronny-150x210mm.htmlhttps://botland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 (https://botland.com.pl/pl/wytrawiacze/1057-wytrawiacz-b327-100g-5901764329183.html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)

4) Zasilanie do RPi
- L7805CV

Przykładowy link do sklepu:

https://abc-rc.pl/product-pol-6839-Elektronika-Stabilizator-L7805CV-5V-1-5A-obudowa-TO-220.ht ml (https://abc-rc.pl/product-pol-6839-Elektronika-Stabilizator-L7805CV-5V-1-5A-obudowa-TO-220.html)

5) Baterie - Model: “18650”

https://botland.com.pl/pl/koszyki-na-baterie/5241-koszyk-na-3-baterie-typu-18650.html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 (https://botland.com.pl/pl/koszyki-na-baterie/5241-koszyk-na-3-baterie-typu-18650.html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)

https://allegro.pl/oferta/ladowarka-baterii-ogniw-18650-2x-akumulator-7858596332(bate rie + akumulator)

https://allegro.pl/oferta/akumulator-ogniwo-2x-bateria-li-ion-18650-10800mah-84049891 41 (https://allegro.pl/oferta/akumulator-ogniwo-2x-bateria-li-ion-18650-10800mah-8404989141)

(same baterie)

6) Goldpiny:

Przykładowy link do sklepu:

https://botland.com.pl/pl/gniazda-szpilkowe-goldpin/204-wtyk-goldpin-2x40-prosty-raster-254mm.html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 (https://botland.com.pl/pl/gniazda-szpilkowe-goldpin/204-wtyk-goldpin-2x40-prosty-raster-254mm.html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)

7) Dioda:

Przykładowy link do sklepu:

https://botland.com.pl/pl/diody-led-rgb/543-dioda-led-5mm-rgb-wsp-anoda.html?search_query=rgb+led+&results=167 (https://botland.com.pl/pl/diody-led-rgb/543-dioda-led-5mm-rgb-wsp-anoda.html?search_query=rgb+led+&results=167)

8) Przyciski:

Przykładowy link do sklepu:

https://botland.com.pl/pl/tact-switch/11138-tact-switch-12x12mm-z-nasadka-kwadrat-czarny-5szt.html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 (https://botland.com.pl/pl/tact-switch/11138-tact-switch-12x12mm-z-nasadka-kwadrat-czarny-5szt.html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)

9) Ekran OLED:

Przykładowy link do sklepu:

https://botland.com.pl/pl/wyswietlacze-i-ekrany/8866-wyswietlacz-oled-niebieski-graficzny-096-128x64px-i2c.html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 (https://botland.com.pl/pl/wyswietlacze-i-ekrany/8866-wyswietlacz-oled-niebieski-graficzny-096-128x64px-i2c.html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)

Budowa maty

Przed rozpoczęciem budowy “maty” najlepiej zapoznać się z schematem i wstępnie rozplanować sobie rozkład połączeń na uniwersalnej płytce.


Pierwszym krokiem będzie rozkład przycisków S1 - S16.
Z racji tego, że wybrana płytka jest dosyć sporych rozmiarów, bo 9cm na 15cm

Okablowanie przycisków:

Następnym krokiem jest połączenie przycisków

Obudowa maty:

Połączenie SSH:

Korzystając z aplikacji na telefon

Końcowy produkt:

Kod do maty

~~ tu wstaw op

## 5. Połączenie robota oraz maty

Opis działania

robot tworzy sieć wifi i ją konfiguruje, mata łączy się z usługą wpisując odpowiedni login i hasło do wifi. po połączeniu mata wysyła string, który zawiera komendy a robot je odpowiednio odczytuje i wykonuje

## 6. Podsumowanie

~~ tu wstaw opis ~~

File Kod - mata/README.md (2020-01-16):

# Krótki opis plików
**Mata.js** - Plik z kodem, który wgrywamy na matę za pomocą odpowiednich komend. Pozwala korzystać z maty do sterowania robotem. Opis jak wgrać kod do maty znajdziesz w poradniku.

**packages.json** - Wymagany plik podczas instalacji pliku z kodem. Zawiera potrzebne biblioteki.

**test_klawiatury_4x4.ino** - Plik do testowania klawiszy w macie w trakcie jej budowy.

**nodeserver.service** - Plik, dzięki którem postawimy serwis na Raspberry.

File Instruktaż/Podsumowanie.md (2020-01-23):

# 6. **Podsumowanie**

Dotarliśmy do końca naszego poradnika. Mamy nadzieję, że spodobał się wam nasz projekt i nie mieliście większych problemów podczas budowy. Poniżej zamieścimy jeszcze listę dodatkowych pomysłów, których nie udało nam się zrealizować.

## **Dodatkowe pomysły**

* **Obudowa robota** - jeśli czujesz, że Twój robot potrzebowałby jednak trochę lepiej wyglądać, możesz zająć się też obudową. Na thingiverse.com jest model podstawy robota, na podstawie którego możesz stworzyć własną obudowę. Nie obejdzie się niestety bez znajomości programu do modelowania np. Autodesk Fusion 360

  * To jest nasz pomysł na wygląd obudowy. Plik z projektem znajdziesz tu [Obudowa](https://github.com/domiipl/Projekt-Inz-Pliki/blob/master/Kod%20-%20robot/Dodatki/Body2.stl)



* **Dodatkowe czujniki** - naszym kolejnym pomysłem było dołożenie czujników, dzięki którym robot wykrywałby przeszkody na drodze. 

* **Emulator maty** - w tym przypadku, jeśli nie masz ochoty budować maty ale interesuje Cię sam robot. Możesz napisać prostą apkę, która emuluje matę. Tym sposobem będziesz w stanie kontrolować swojego robota z aplikacji na komputerze.

* **Klocki zamiast przycisków** - zamiast przycisku w macie, możesz spróbować stworzyć klocki które po włożeniu w otwór będą działały tak samo jak przyciski. Proponujemy odczytywanie rodzaju klocka za pomocą RFID lub oporników.

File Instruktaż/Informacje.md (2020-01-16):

# 1. **Informacje o projekcie**

Projekt dzieli się na trzy części. Robota, interaktywną matę oraz poradnik z opisem budowy projektu.

Robot jest pojazdem, który odbiera odpowiednie komendy i wykonuje odebraną sekwencję. Za odczytywanie a następnie wykonywanie komend odpowiada włożony do robota NodeMCU, zwany powszechnie Arduino. 

Interaktywna mata posiada osiemnaście przycisków, z czego szesnaście z nich odpowiada za sterowanie robotem a pozostałe dwa są przyciskami funkcyjnymi. Za wysłanie odpowiednio zaprogramowanych komend odpowiada Raspberry Pi Zero.

W naszym projekcie to robot odpowiada za utworzenie HotSpotu WiFi, do którego następnie łączymy się z maty. 

Jesteśmy w stanie sterować robotem w dwóch trybach. Pierwszym z nich jest tryb komend. W danym trybie mamy do dyspozycji szesnaście przycisków. Każdy z przycisków jesteśmy w stanie zaprogramować na pięć sposobów, a są to:

* Ruch do przodu - pojazd przejedzie pewien dystans do przodu,
* Ruch do tyłu - pojazd przejedzie pewien dystans do tyłu,
* Obrót w lewo - pojazd obróci się o 90 stopni w lewo,
* Obrót w prawo - pojazd obróci się o 90 stopni w prawo,
* Pusta komenda - robot nie wykona ruchu.

Kiedy zaprogramujemy swoją sekwencję komend na macie, wciskamy przycisk "Start", który po naciśnięciu wyśle odpowiednie znaki do robota. Robot następnie odczyta odebrane znaki i wykona ruch zgodny z zaprogramowaną sekwencją na macie. Drugi z wymienionych trybów jest trybem jazdy swobodnej. W danym trybie mamy do dyspozycji cztery przyciski koloru niebieskiego, które jak w przypadku wyżej również odpowiadają za poruszanie pojazdem, tym razem w czasie rzeczywistym. Po naciśnięciu dowolnego przycisku pojazd poruszy lub obróci się w wybranym przez nas kierunku. Do zmiany trybu robota służy drugi z przycisków funkcyjnych na macie.

W projekcie zamieściliśmy również poradnik, ze szczegółowym opisem jak zbudować nasz zestaw. Poradnik zawiera:

* Listę wymaganych przedmiotów, w które warto się zaopatrzyć przed przystąpieniem do budowy,
* Szczegółowy opis budowy robota oraz maty,
* Opisy kodów wymaganych do sterowania pojazdem oraz matą,
* Opis własnoręcznego tworzenia płytek pcb,
* Dodatkowe pomysły, które można dołączyć do projektu.

Projekt jest projektem otwartym, jeśli ktoś zdecyduje się na budowę, powinien być w stanie go skonstruować korzystając z instruktażu.

Warto w tym miejscu jeszcze dodać, że decydując się na budowę projektu trzeba się liczyć z pewnymi kosztami. Orientacyjne ceny na dzień 16 stycznia 2020 roku to:

* Robot - około 130 złotych,
* Mata - około 205 złotych.

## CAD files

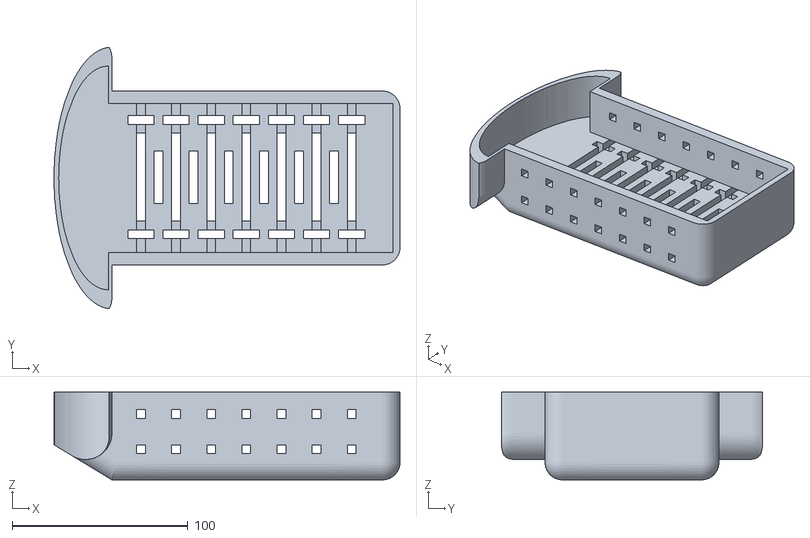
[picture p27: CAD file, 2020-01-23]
Kod - robot/Dodatki/Body2.stl
197.0 x 148.8 x 50.0

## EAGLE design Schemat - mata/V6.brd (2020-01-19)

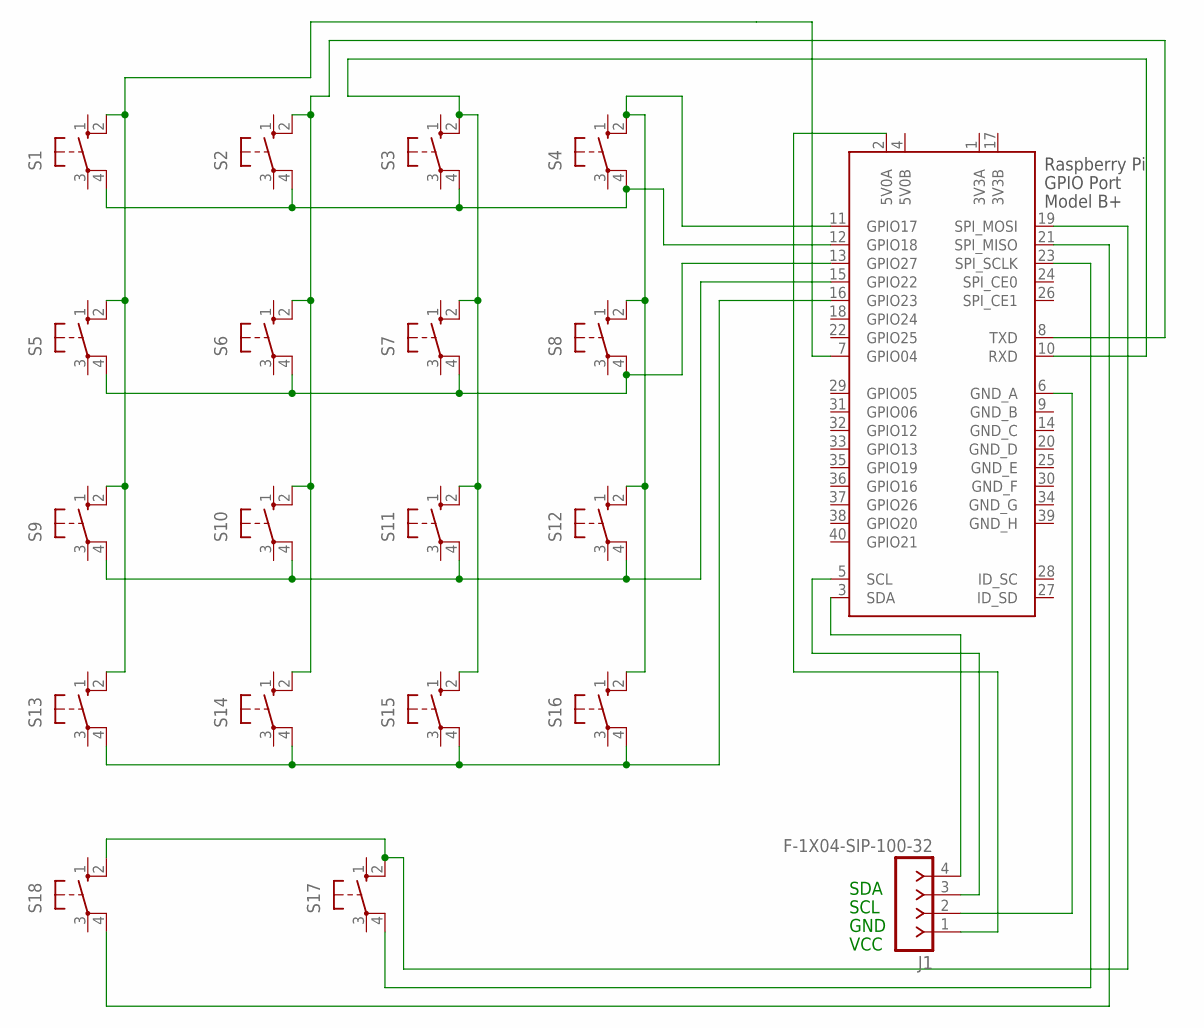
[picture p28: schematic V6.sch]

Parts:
J1: F-1X04-SIP-100-32; SIP-100-04-32
S1, S2, S3, S4, S5, S6, S7, S8, S9, S10, S11, S12, S13, S14, S15, S16, S17, S18: 40-XX; B3F-40XX
X1: RASPI_GPIO_B+#_PIN; RASPI_GPIO_B+_PIN

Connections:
3V3A: X1.1 (3V3A)
3V3B: X1.17 (3V3B)
5V0B: X1.4 (5V0B)
GND_B: X1.9 (GND_B)
GND_C: X1.14 (GND_C)
GND_D: X1.20 (GND_D)
GND_E: X1.25 (GND_E)
GND_F: X1.30 (GND_F)
GND_G: X1.34 (GND_G)
GND_H: X1.39 (GND_H)
unnamed: S1.2 (S1), S5.2 (S1), S9.2 (S1), S13.2 (S1), X1.7 (GPIO04)
unnamed: S2.2 (S1), S6.2 (S1), S10.2 (S1), S14.2 (S1), X1.8 (TXD)
unnamed: J1.1, X1.2 (5V0A)
unnamed: J1.4, X1.3 (SDA)
unnamed: S13.4 (P1), S14.4 (P1), S15.4 (P1), S16.4 (P1), X1.16 (GPIO23)
unnamed: S9.4 (P1), S10.4 (P1), S11.4 (P1), S12.4 (P1), X1.15 (GPIO22)
unnamed: S5.4 (P1), S6.4 (P1), S7.4 (P1), S8.4 (P1), X1.13 (GPIO27)
unnamed: S1.4 (P1), S2.4 (P1), S3.4 (P1), S4.4 (P1), X1.12 (GPIO18)
unnamed: S3.2 (S1), S7.2 (S1), S11.2 (S1), S15.2 (S1), X1.10 (RXD)
unnamed: S18.4 (P1), X1.21 (SPI_MISO)
unnamed: S17.4 (P1), X1.23 (SPI_SCLK)
unnamed: J1.3, X1.5 (SCL)
unnamed: J1.2, X1.6 (GND_A)
unnamed: S17.2 (S1), S18.2 (S1), X1.19 (SPI_MOSI)
unnamed: S4.2 (S1), S8.2 (S1), S12.2 (S1), S16.2 (S1), X1.11 (GPIO17)

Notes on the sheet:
SDA
SCL
GND
VCC

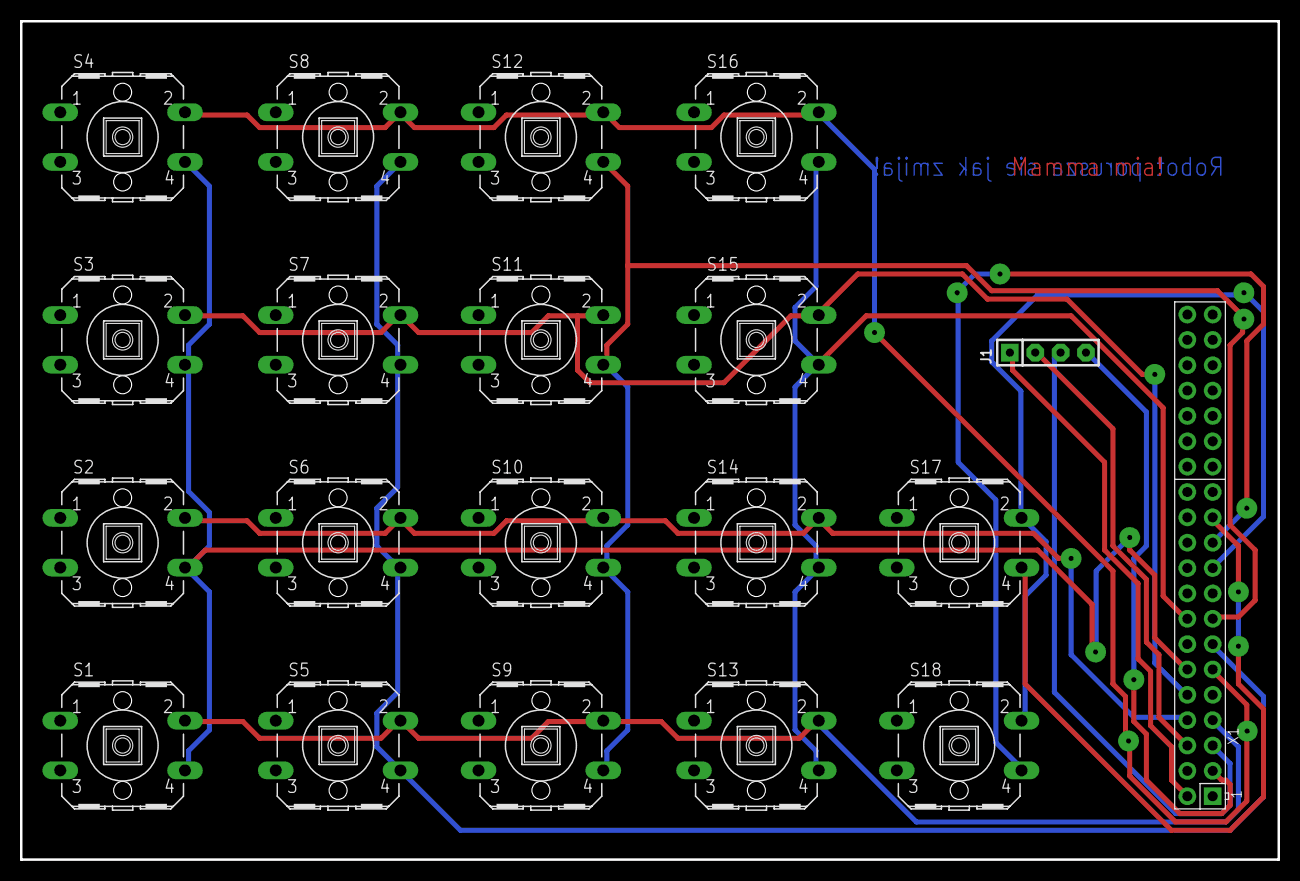
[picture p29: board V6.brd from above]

Board: 2 copper layers, 126.0 x 84.0 mm, 20 parts (0 on the bottom side), 15 nets.

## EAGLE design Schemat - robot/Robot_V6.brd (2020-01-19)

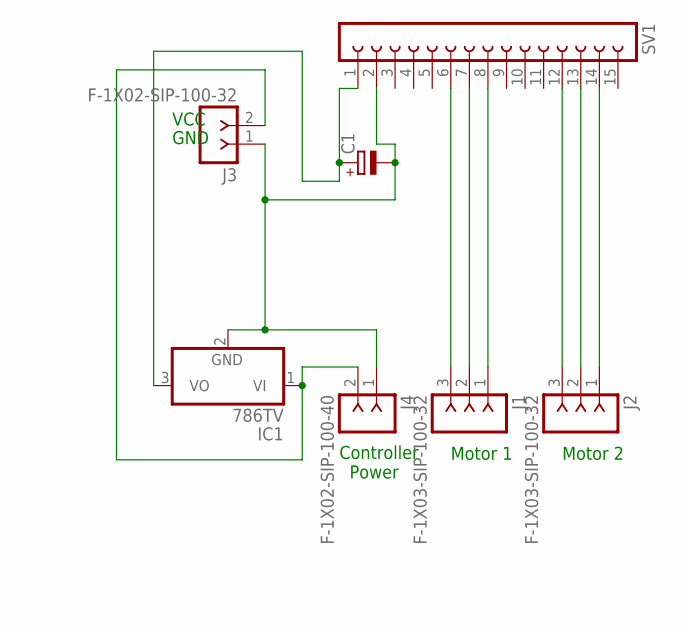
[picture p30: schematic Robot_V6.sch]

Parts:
C1: CPOL-EUE1.8-4; E1,8-4
IC1: 786TV; TO220V
J1, J2: F-1X03-SIP-100-32; SIP-100-03-32
J3: F-1X02-SIP-100-32; SIP-100-02-32
J4: F-1X02-SIP-100-40; SIP-100-02-40
SV1: FE15-1; FE15

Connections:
unnamed: C1.-, IC1.2 (GND), J3.1, J4.1, SV1.2
unnamed: J2.1, SV1.14
unnamed: J2.2, SV1.13
unnamed: J2.3, SV1.12
unnamed: J1.1, SV1.8
unnamed: J1.2, SV1.7
unnamed: J1.3, SV1.6
unnamed: IC1.1 (VI), J3.2, J4.2
unnamed: C1.+, IC1.3 (VO), SV1.1

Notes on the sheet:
Motor 1
Motor 2
VCC
GND
Controller Power

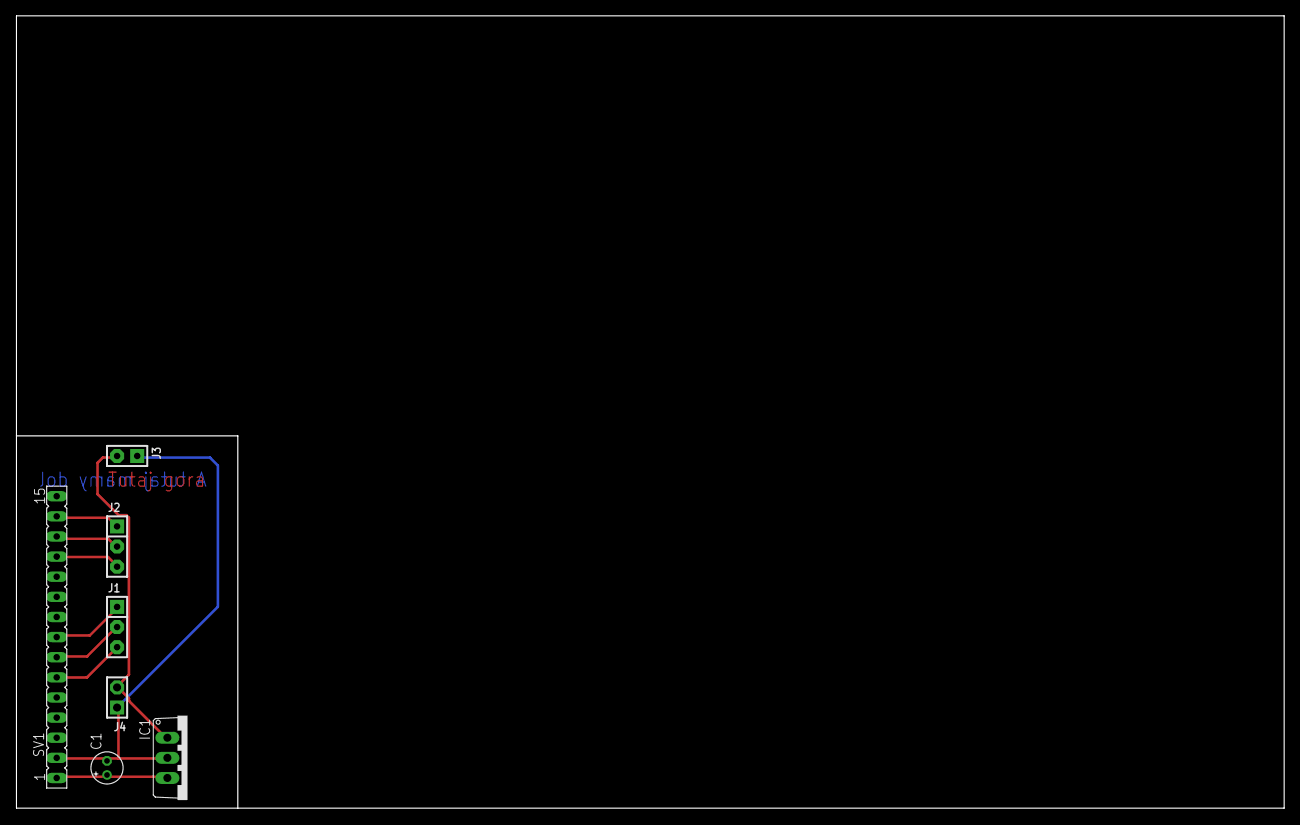
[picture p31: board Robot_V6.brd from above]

Board: 2 copper layers, 160.0 x 100.0 mm, 7 parts (0 on the bottom side), 9 nets.

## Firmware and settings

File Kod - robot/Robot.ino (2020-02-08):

#include <ESP8266WiFi.h>

#ifndef APSSID
#define APSSID "Robot"
#endif
#ifndef PORT 
#define PORT 12345
#endif

WiFiServer server(PORT);
const char *ssid = APSSID;
const char *pass = "RobotZmija987";
int IN1=12;   
int IN2=14;   
int IN3=4;    
int IN4=5;   
int ENA=0;    
int ENB=13;   
int multi_= 5;
int time_= 25;
int led=2;    
bool fDrive = false;


void drive(int I1, int I2, int I3, int I4, int multi, int t){
  digitalWrite(IN1,I1);
  digitalWrite(IN2,I2);
  digitalWrite(IN3,I3);
  digitalWrite(IN4,I4);
  Serial.println("Akceleracja:");
  for(int i = 0; i < 1024; i += multi){
    analogWrite(ENA,i);
    analogWrite(ENB,i);
    Serial.print(i);
    Serial.print("...");
    delay(1);
  }
  delay(t);
  Serial.println("Hamowanie:");
  for(int i = 1024; i > 0; i -= multi){
    analogWrite(ENA,i);
    analogWrite(ENB,i);
    Serial.print(i);
    Serial.print("...");
    delay(1);
  }
  digitalWrite(IN1,LOW);
  digitalWrite(IN2,LOW);
  digitalWrite(IN3,LOW);
  digitalWrite(IN4,LOW);
  delay(500);
}
void turn(int I1, int I2, int I3, int I4, int t){
  digitalWrite(IN1,I1);
  digitalWrite(IN2,I2);
  digitalWrite(IN3,I3);
  digitalWrite(IN4,I4);
  analogWrite(ENA,400);
  analogWrite(ENB,400);
  delay(700);
  digitalWrite(IN1,LOW);
  digitalWrite(IN2,LOW);
  digitalWrite(IN3,LOW);
  digitalWrite(IN4,LOW);
  analogWrite(ENA,0);
  analogWrite(ENB,0);
  delay(500);
}
void freeDrive(int I1, int I2, int I3, int I4, int spd){
  analogWrite(ENA,spd);
  analogWrite(ENB,spd);
  digitalWrite(IN1,I1);
  digitalWrite(IN2,I2);
  digitalWrite(IN3,I3);
  digitalWrite(IN4,I4);
}

void setup(){
  pinMode(IN1,OUTPUT); 
  pinMode(IN2,OUTPUT); 
  pinMode(IN3,OUTPUT); 
  pinMode(IN4,OUTPUT); 
  pinMode(ENA,OUTPUT); 
  pinMode(ENB,OUTPUT); 
  WiFi.mode(WIFI_STA); 
  WiFi.disconnect(); 
  delay(100);
  
  Serial.begin(115200);
  Serial.println();
  Serial.print("Konfiguracja AP...");
  
  IPAddress ip(192,168,1,200);
  IPAddress gateway(192,168,1,254);
  IPAddress subnet(255,255,255,0);
  WiFi.softAPConfig(ip, gateway, subnet);
  WiFi.softAP(ssid,pass,1,false,1);
  IPAddress myIP = WiFi.softAPIP(); 
  Serial.print("AP IP: "); 
  Serial.println(myIP);          
  
  server.begin(); 

  digitalWrite(IN1,LOW); 
  digitalWrite(IN2,LOW); 
  digitalWrite(IN3,LOW); 
  digitalWrite(IN4,LOW); 
  analogWrite(ENA,0);
  analogWrite(ENB,0);
}


void loop(){
  WiFiClient client = server.available();
  
  if (client){
    if(client.connected()){
      Serial.println("Client Connected");
    }
    while(client.connected()){
      while(client.available()>0){
        int readed = client.read();
          switch(readed){
            case 'u':
              fDrive = false;
              drive(HIGH, LOW, HIGH, LOW, 5, 1024);
              break;
            case 'd':
              fDrive = false;
              drive(LOW, HIGH, LOW, HIGH, 5, 1024);
              break;
            case 'l':
              fDrive = false;
              turn(LOW, HIGH, HIGH, LOW, 450);
              break;
            case 'r':
              fDrive = false;
              turn(HIGH, LOW, LOW, HIGH, 450);
              break;
            case 'z':
              fDrive = true;
              freeDrive(HIGH, LOW, HIGH, LOW, 1024);
              break;
            case 'x':
              fDrive = true;
              freeDrive(LOW, HIGH, LOW, HIGH, 1024);
              break;
            case 'c':
              fDrive = true;
              freeDrive(LOW, HIGH, HIGH, LOW, 1024);
              break;
            case 'v':
              fDrive = true;
              freeDrive(HIGH, LOW, LOW, HIGH, 1024);
              break;
            case 's':
              fDrive = false;
              digitalWrite(IN1,LOW); 
              digitalWrite(IN2,LOW); 
              digitalWrite(IN3,LOW); 
              digitalWrite(IN4,LOW); 
              analogWrite(ENA,0);
              analogWrite(ENB,0);
              break;              
            default:
              if(!fDrive){
                digitalWrite(IN1,LOW); 
              digitalWrite(IN2,LOW); 
              digitalWrite(IN3,LOW);
              digitalWrite(IN4,LOW); 
              }
              break;
          }
        //}
      //Send Data to connected client
      while(Serial.available()>0){
        client.write(Serial.read());
      }
    }
  }
  client.stop();
  Serial.println("Client disconnected");    
  }
}

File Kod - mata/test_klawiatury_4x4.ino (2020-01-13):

#include <Keypad.h> //biblioteka od klawiatury
 
const byte ROWS = 4; // ile wierszy
const byte COLS = 4; //ile kolumn
 
byte rowPins[ROWS] = {5, 4, 3, 2}; //piny wierszy
byte colPins[COLS] = {6, 7, 8, 9}; //piny kolum
 
char keys[ROWS][COLS] = { //mapowanie klawiatury
  {'1','2','3','A'},
  {'4','5','6','B'},
  {'7','8','9','C'},
  {'*','0','#','D'}
};
 
Keypad klawiatura = Keypad( makeKeymap(keys), rowPins, colPins, ROWS, COLS ); //inicjalizacja klawiatury
 
void setup(){
  Serial.begin(9600);
}
  
void loop(){
  char klawisz = klawiatura.getKey();
  
  if (klawisz){
    Serial.println(klawisz);
  }
}

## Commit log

2020-01-07 potrzebne materiały
    [Robot_v2.brd, Robot_v2.sch, V3.brd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]
2020-01-15 mata - zly pin
2020-01-17 aktualizacja schematów
    [V5.brd, V5.sch]
2020-01-23 projekt obudowy
    [Body2.stl]

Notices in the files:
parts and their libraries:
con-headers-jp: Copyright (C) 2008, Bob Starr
